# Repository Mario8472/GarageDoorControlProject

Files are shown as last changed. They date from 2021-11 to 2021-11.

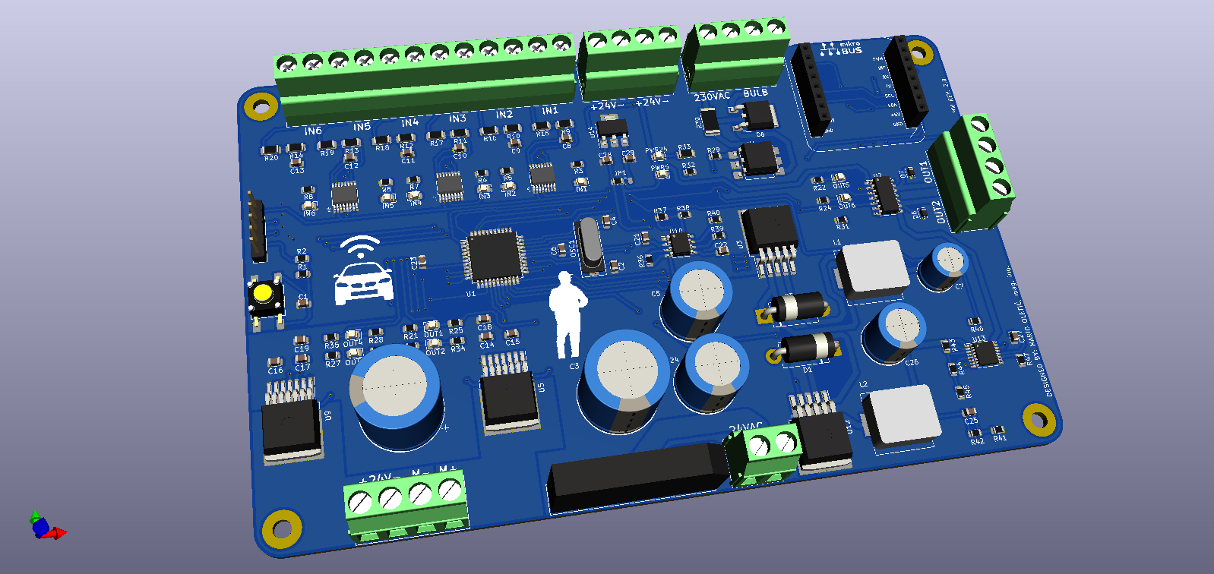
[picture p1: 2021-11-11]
KiCAD/Pictures/GarageDoorControl2.png

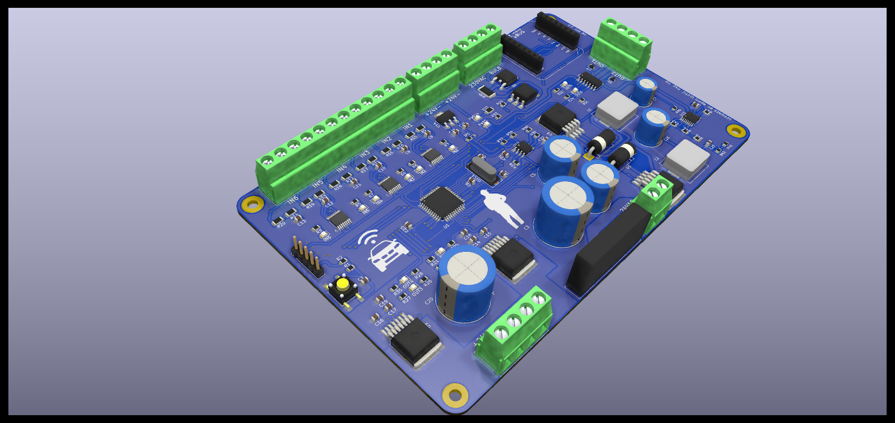
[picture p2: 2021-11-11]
KiCAD/Pictures/GarageDoorControl8.png

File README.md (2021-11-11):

# GarageDoorControlProject
Hardware and Software for Garage door control (retrofit) 

   Project:    Garage Door Control Unit
   MCU:        PIC18F45K22
   Hardware:   Garage Door Control PCB Card
   Software:   mikroC PRO for PIC18
   Author:     Mario Oletić
   
   Project description:
   -----------------------------------------------------------------------------
   This project is developed (both hardware and software) for replacing/retrofit
   the old garage door PCB. PCB has six input signals (24VDC level). Two of 
   them are used for starting the door movements (opening or closing). Doors can
   be started with radio switch (Input1) with 24VDC signal output or some other 
   common switch (Input2). Other four inputs are used for external capacitive or
   inductive sensors to determine door position - two for UP and DOWN positions 
   and two to determine a position of doors while approaching CLOSE or OPEN 
   positions. The last two positions are used for slowing the doors down. 
   Signals on INPUT1 and INPUT2 are switching between four working modes. MODE 0 
   and MODE2 are for stoping, MODE1 for opening and MODE3 for closing the doors.
   Outputs are used for controlling the 24V DC motor with PWM signals. Depending 
   on the door position, the motor can rotate with two different speeds (speed 
   depends on the PWM duty cycle) - one is for normal door speed and the other 
   (slower) is for approaching final positions. Also, when activating the door, 
   lights turn on. There are two outputs for 24V DC LED lights and one output 
   for 230V AC light bulb which is controlled via Triac. Triac is triggered with 
   OptoTriac IC with zero-cross detection circuit. Also, OptoTriac isolates 230V 
   AC system from the rest of the PCB low voltage systems. Lights will be turned 
   off after doors are stoped, no matter in what position, after a fixed period 
   of time passes. When doors are not moving, MCU goes into sleep mode with much 
   lower current consumption. When a new signal for activating the doors appears, 
   MCU wakes up.

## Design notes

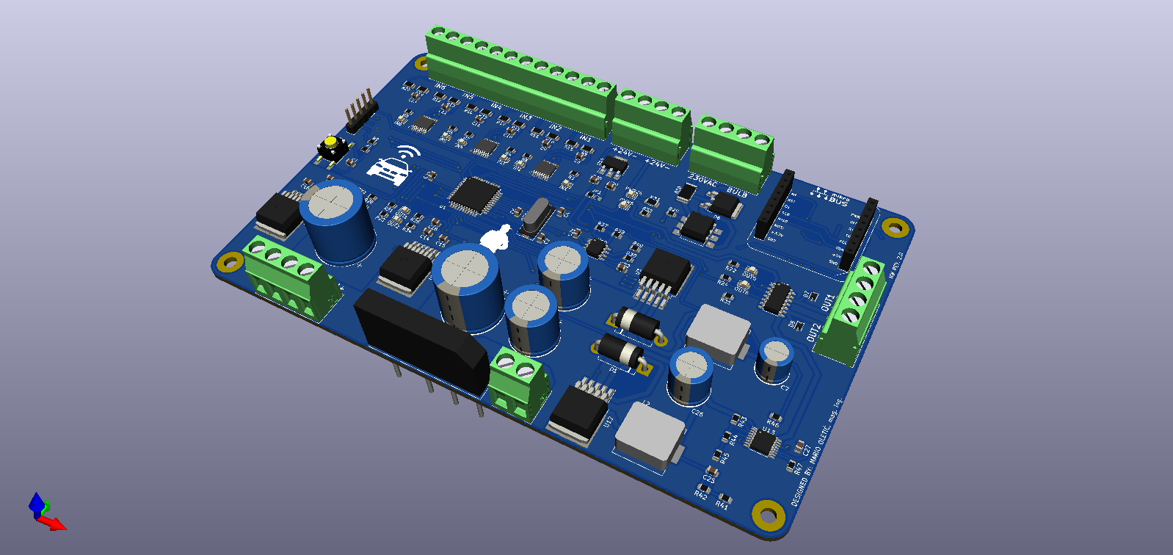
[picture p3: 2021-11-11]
KiCAD/Pictures/GarageDoorControl9.png

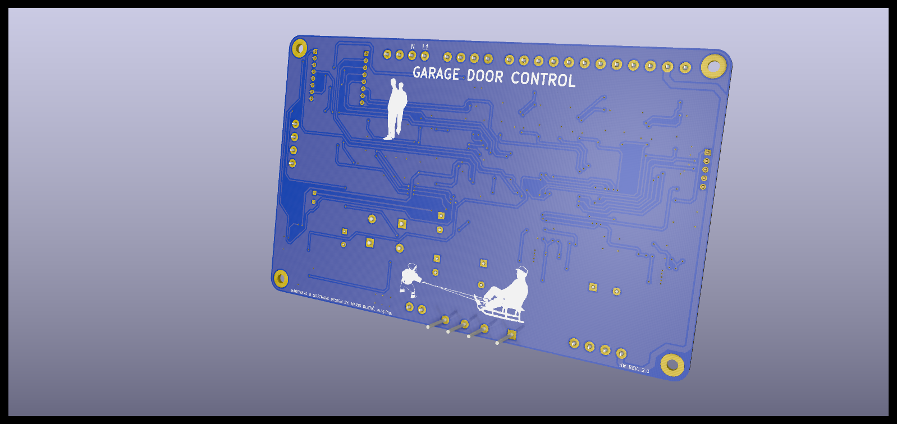
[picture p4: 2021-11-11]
KiCAD/Pictures/GarageDoorControl18.png

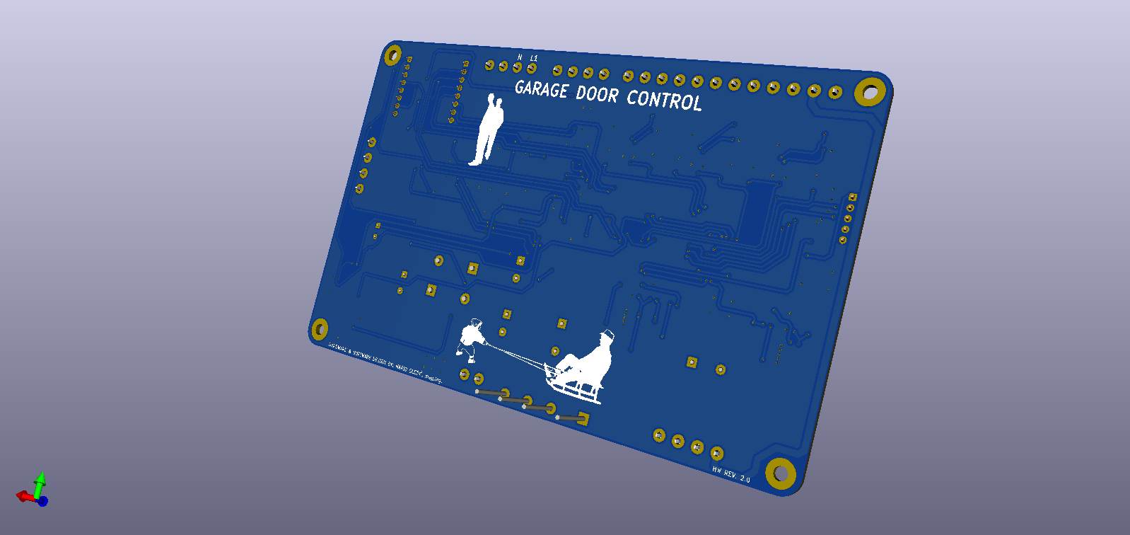
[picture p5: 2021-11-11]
KiCAD/Pictures/GarageDoorControl20.png

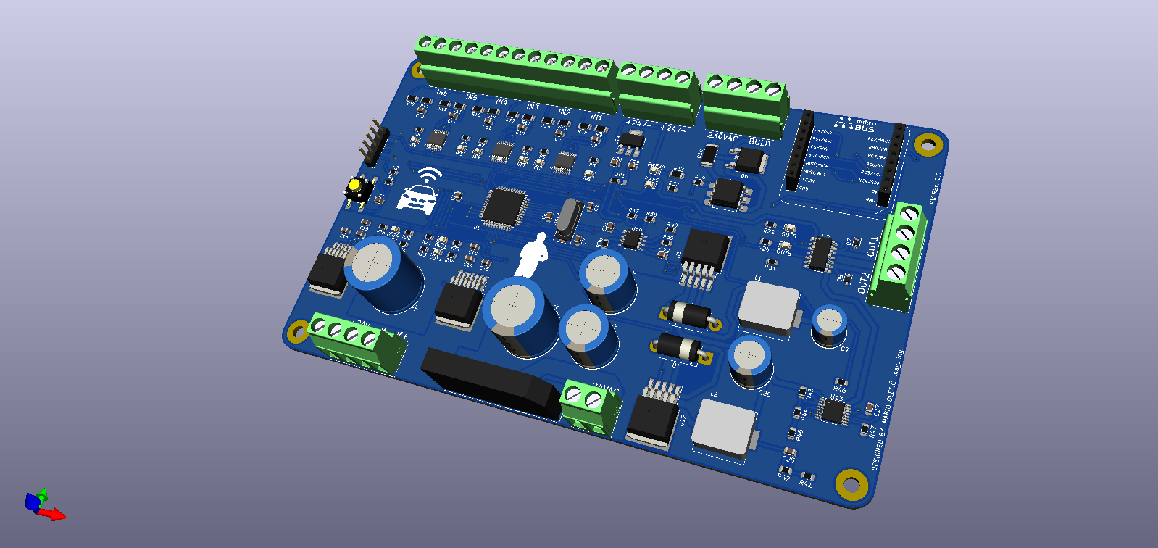
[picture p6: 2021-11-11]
KiCAD/Pictures/GarageDoorControl16.png

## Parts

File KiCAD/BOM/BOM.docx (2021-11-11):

BOM – Garage Door Control

Id | Designator | Package | Qt. | Designation
1 | G*** | dam5 | 1 | LOGO
2 | G*** | me_logo | 1 | LOGO
3 | G*** | m&d_logo | 1 | LOGO
4 | OSC1 | Crystal_SMD_HC49-SD | 1 | 8MHz
5 | U13 | HTSSOP-16-1EP_4.4x5mm_P0.65mm_EP3x3mm | 1 | TPS26600
6 | G*** | car_logo | 1 | LOGO
7 | C1,C6,C23 | C_0805_2012Metric | 3 | 100nF
8 | C2,C4 | C_0805_2012Metric | 2 | 22pF
9 | C3 | CP_Radial_D16.0mm_P7.50mm | 1 | 2200uF
10 | C7 | CP_Radial_D8.0mm_P3.50mm | 1 | 180uF
11 | C8,C9,C10,C11,C12,C13 | C_0805_2012Metric | 6 | 10nF
12 | CN1 | mikroBUS_socket | 1 | mikroBUS_socket
13 | D5,D1 | D_DO-201AD_P12.70mm_Horizontal | 2 | D_Schottky
14 | D6 | TO-252-2 | 1 | Q_TRIAC_A1A2G
15 | IN1,IN2,IN3,IN4,IN5,IN6, OUT1,OUT2,OUT3,OUT4, OUT5,OUT6,PWR5,PWR24 | LED_0805_2012Metric | 14 | LED
16 | J1 | PinHeader_1x05_P2.54mm_Vertical | 1 | Conn_01x05
17 | J2 | PCB_Screw_Terminal_5.08_12ways | 1 | Screw_Terminal_01x12
18 | L1 | HPI1206 | 1 | 68uH
19 | R1,R25,R27,R34,R35,R38, R39,R40,R46 | R_0805_2012Metric | 9 | 10k
20 | R2 | R_0805_2012Metric | 1 | 2k2
21 | R3,R4,R5,R6,R7,R8,R21,R22,R23,R24,R26,R28,R32 | R_0805_2012Metric | 13 | 4k7
22 | R9,R10,R11,R12,R13,R14, R15,R16,R17,R18,R19,R20 | R_1206_3216Metric | 12 | 330
23 | R29 | R_0805_2012Metric | 1 | 330
24 | R30 | R_2512_6332Metric | 1 | 200
25 | R31 | R_0805_2012Metric | 1 | 150
26 | R33 | R_1206_3216Metric | 1 | 10k
27 | RS1 | TACTSWITCH6x6 | 1 | SW_Push
28 | U2 | SOIC-14_3.9x8.7mm_P1.27mm | 1 | BTS5120G
29 | U3 | TO-263-5_TabPin3 | 1 | LM2596S-5
30 | U4 | SMDIP-6_W9.53mm | 1 | VO3062
31 | U6,U7,U8 | ISO1212 | 3 | ISO1212
32 | D7,D8 | D_SOD-323 | 2 | D
33 | C14,C15,C16,C17 | C_0805_2012Metric | 4 | 0.22uF
34 | C18,C19 | C_0805_2012Metric | 2 | 0.1uF
35 | C20 | CP_Radial_D16.0mm_P7.50mm | 1 | 1000uF
36 | U5,U9 | TO-263-7_TabPin4 | 2 | BTN8982TA
37 | C21 | C_0805_2012Metric | 1 | 0.1nF
38 | C22 | C_0805_2012Metric | 1 | 100uF
39 | R36 | R_0805_2012Metric | 1 | 100k
40 | R37 | R_0805_2012Metric | 1 | 47k
41 | U10 | SOIC-8_3.9x4.9mm_P1.27mm | 1 | TPS25921A
42 | H1,H2,H3,H4 | ScrewHoleM3 | 4 | ScrewHoleM3
43 | J4,J5,J6,J7 | PCB_Screw_Terminal_5.08_4ways | 4 | Screw_Terminal_01x04
44 | J3 | PCB_Screw_Terminal_5.08_2ways | 1 | Screw_Terminal_01x02
45 | U1 | TQFP-44_10x10mm_P0.8mm | 1 | PIC18F45K22
46 | U11 | DiodeBridge_GBI | 1 | GBI25B
47 | C5,C24 | CP_Radial_D12.5mm_P5.00mm | 2 | 680uF
48 | C25 | C_0805_2012Metric | 1 | 560pF
49 | C26 | CP_Radial_D10.0mm_P5.00mm | 1 | 150uF
50 | L2 | HPI1206 | 1 | 47uH
51 | R41 | R_0805_2012Metric | 1 | 1k
52 | R42 | R_0805_2012Metric | 1 | 18k5
53 | U12 | TO-263-5_TabPin3 | 1 | LM2596S-ADJ
54 | C27 | C_0805_2012Metric | 1 | 2.2uF
55 | R43 | R_0805_2012Metric | 1 | 715k
56 | R44 | R_0805_2012Metric | 1 | 20k
57 | R45 | R_0805_2012Metric | 1 | 30.1k
58 | R47 | R_0805_2012Metric | 1 | 5,36k
59 | C28 | C_0805_2012Metric | 1 | 0.47uF
60 | C29 | C_0805_2012Metric | 1 | 33uF
61 | JP1 | Jumper_0805 | 1 | SolderJumper_3_Open
62 | U14 | SOT-223 | 1 | LM3940

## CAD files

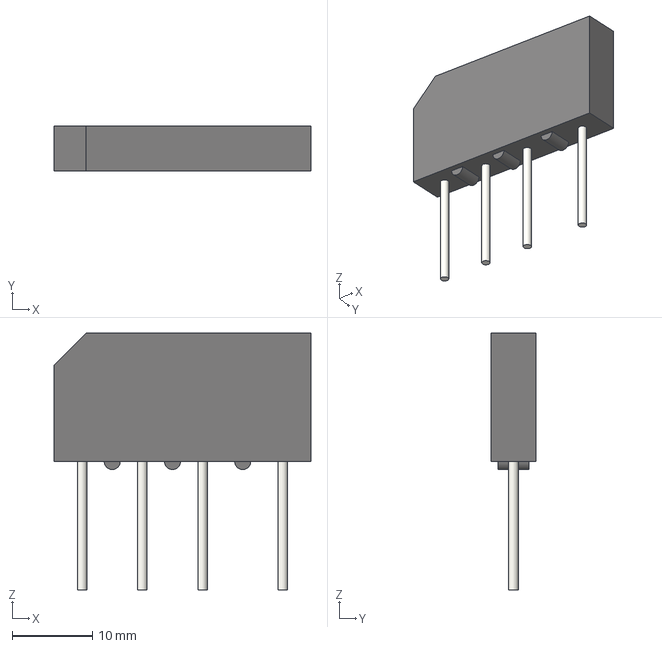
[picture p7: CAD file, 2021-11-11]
KiCAD/3D models/Diode_Bridge_32.0x5.6x17.0mm_P10.0mm_P7.5mm.step
32.0 x 5.60 x 32.0 mm

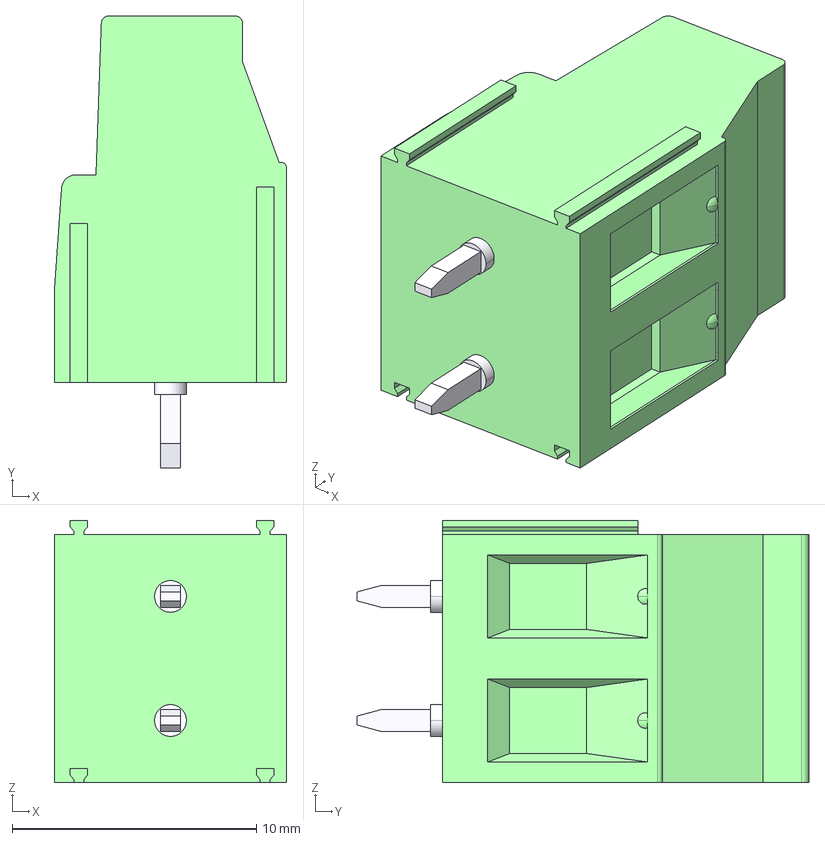
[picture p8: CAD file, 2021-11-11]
KiCAD/3D models/PCB Terminal 5.08 - 2way.stp
9.50 x 18.5 x 10.7 mm

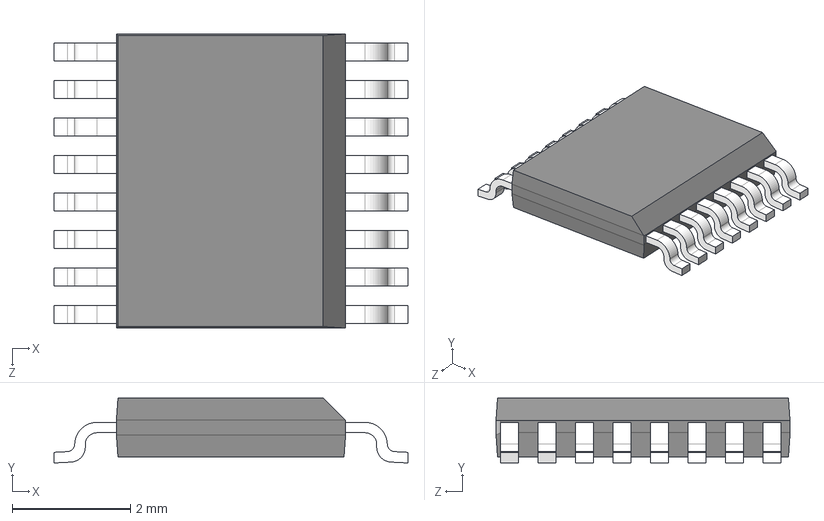
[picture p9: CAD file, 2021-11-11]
KiCAD/3D models/SSOP16.STEP
5.99 x 1.10 x 4.98 mm

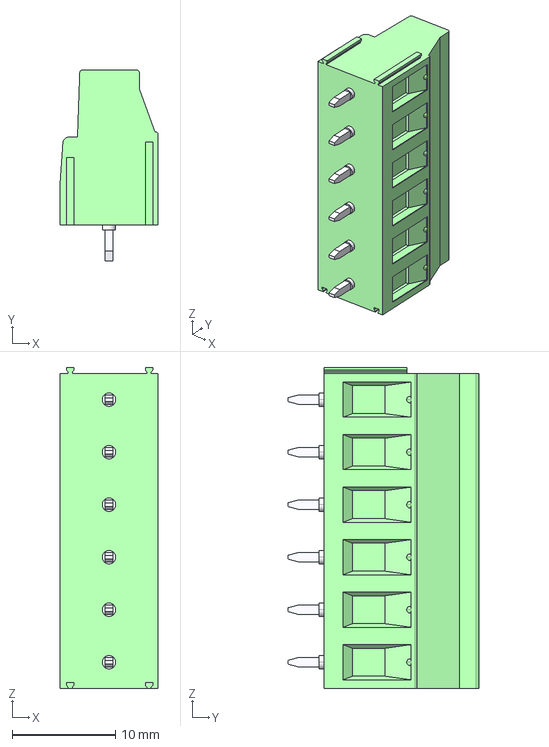
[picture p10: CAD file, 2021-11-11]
KiCAD/3D models/PCB Terminal 5.08 - 6way.stp
9.50 x 18.5 x 31.0 mm

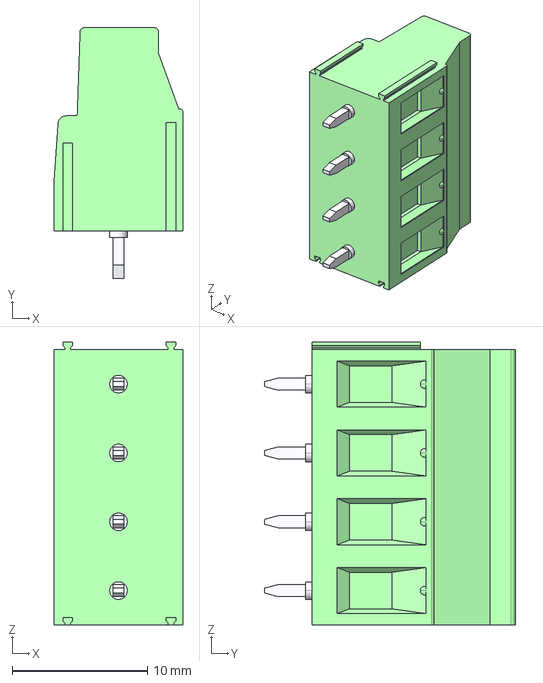
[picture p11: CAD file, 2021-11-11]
KiCAD/3D models/PCB Terminal 5.08 - 4way.stp
9.50 x 18.5 x 20.9 mm

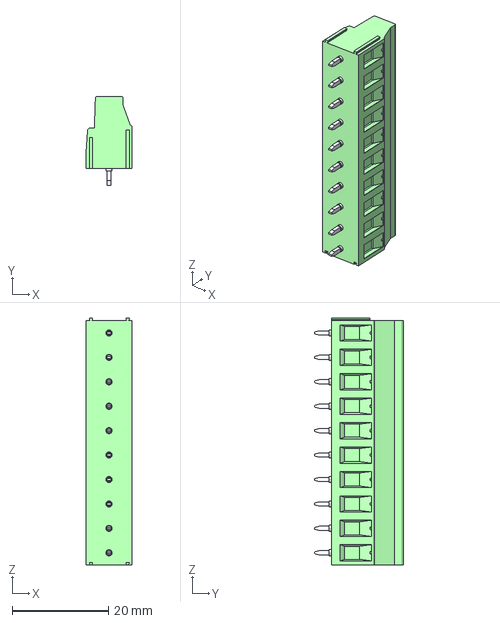
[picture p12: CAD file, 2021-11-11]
KiCAD/3D models/PCB Terminal 5.08 - 10way.stp
9.50 x 18.5 x 51.4 mm

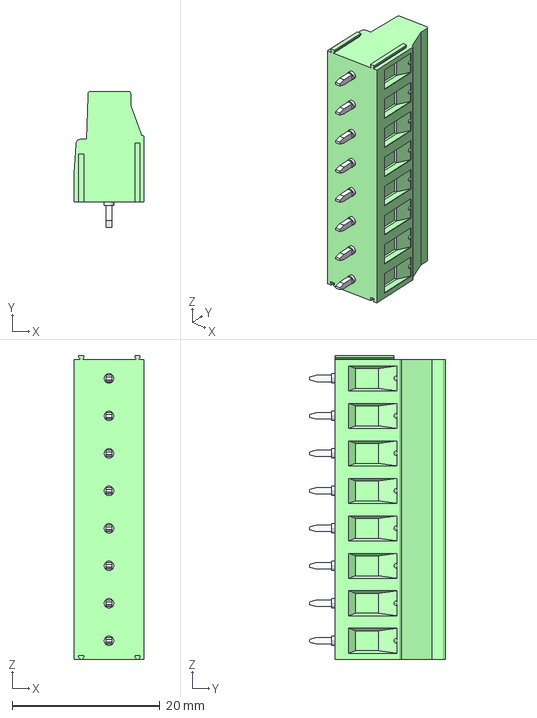
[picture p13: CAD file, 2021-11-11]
KiCAD/3D models/PCB Terminal 5.08 - 8way.stp
9.50 x 18.5 x 41.2 mm

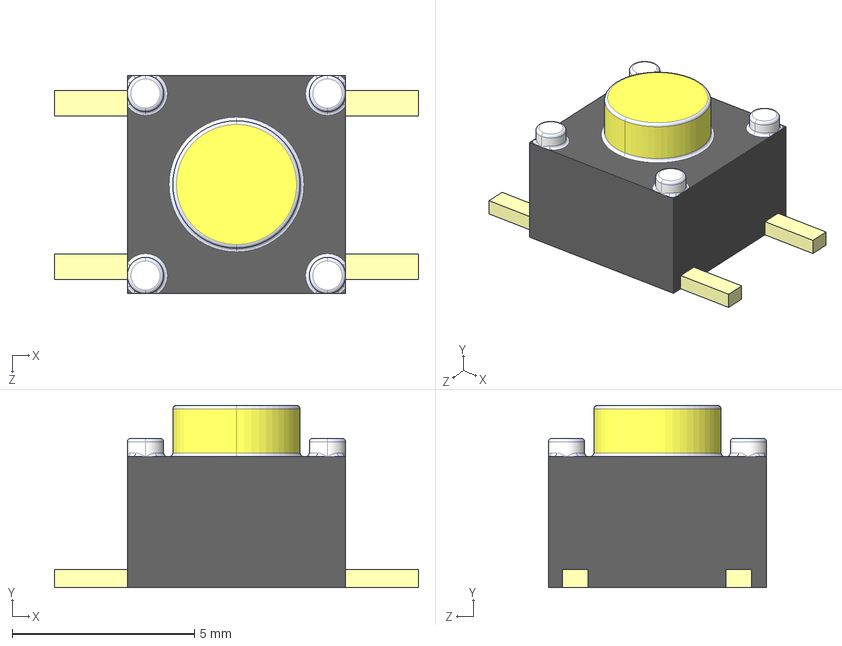
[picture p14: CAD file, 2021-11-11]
KiCAD/3D models/TACT SWITCH SMD 6X6.STEP
10.0 x 5.00 x 6.00 mm

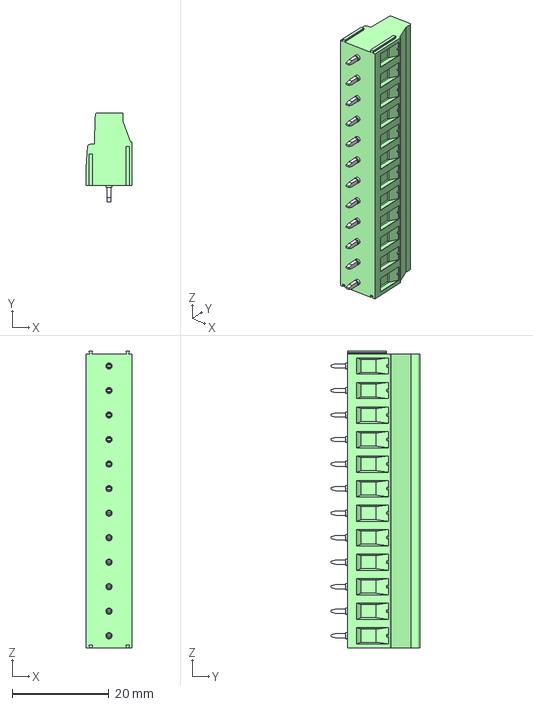
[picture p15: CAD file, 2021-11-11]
KiCAD/3D models/PCB Terminal 5.08 - 12way.stp
9.50 x 18.5 x 61.5 mm

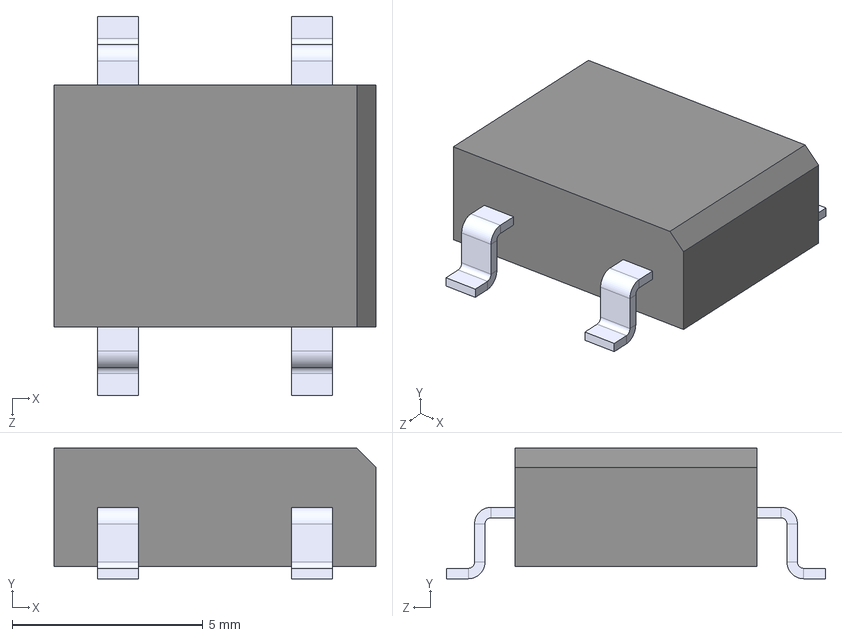
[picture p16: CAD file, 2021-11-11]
KiCAD/3D models/DB207S.SLDPRT.STEP
8.45 x 3.43 x 9.95 mm

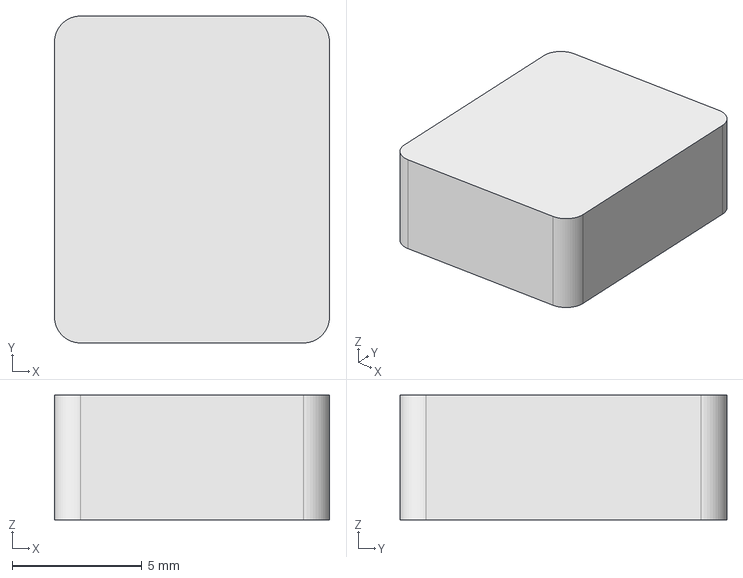
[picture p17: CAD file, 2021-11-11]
KiCAD/3D models/hpis.step
10.6 x 12.6 x 4.80 mm

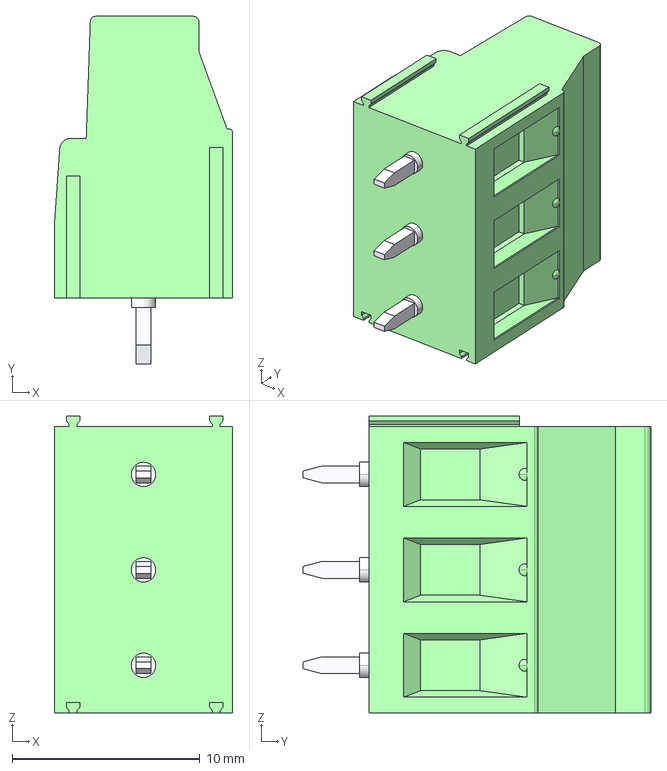
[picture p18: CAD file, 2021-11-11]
KiCAD/3D models/PCB Terminal 5.08 - 3way.stp
9.50 x 18.5 x 15.8 mm

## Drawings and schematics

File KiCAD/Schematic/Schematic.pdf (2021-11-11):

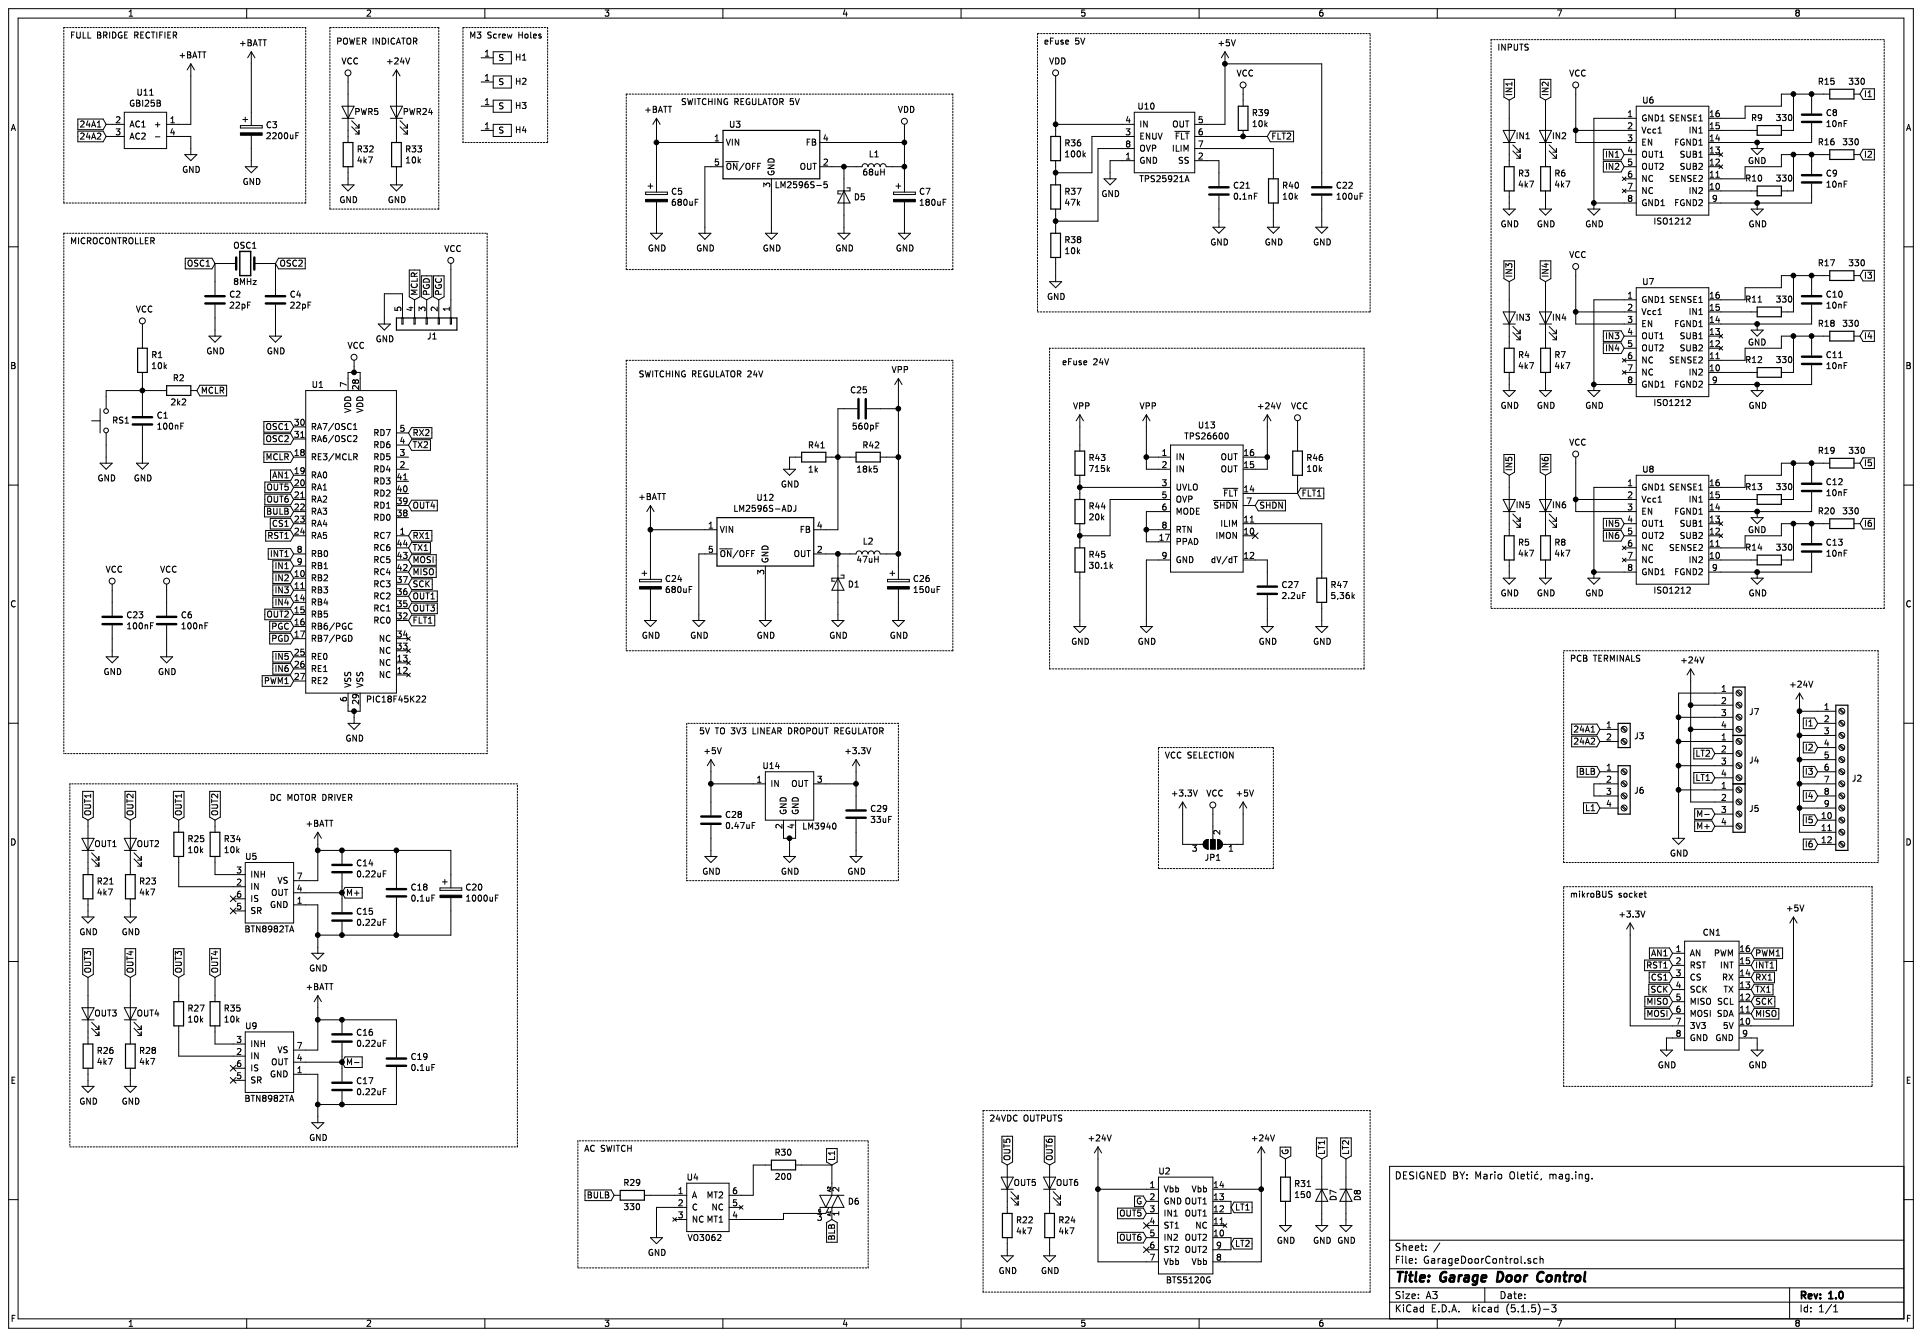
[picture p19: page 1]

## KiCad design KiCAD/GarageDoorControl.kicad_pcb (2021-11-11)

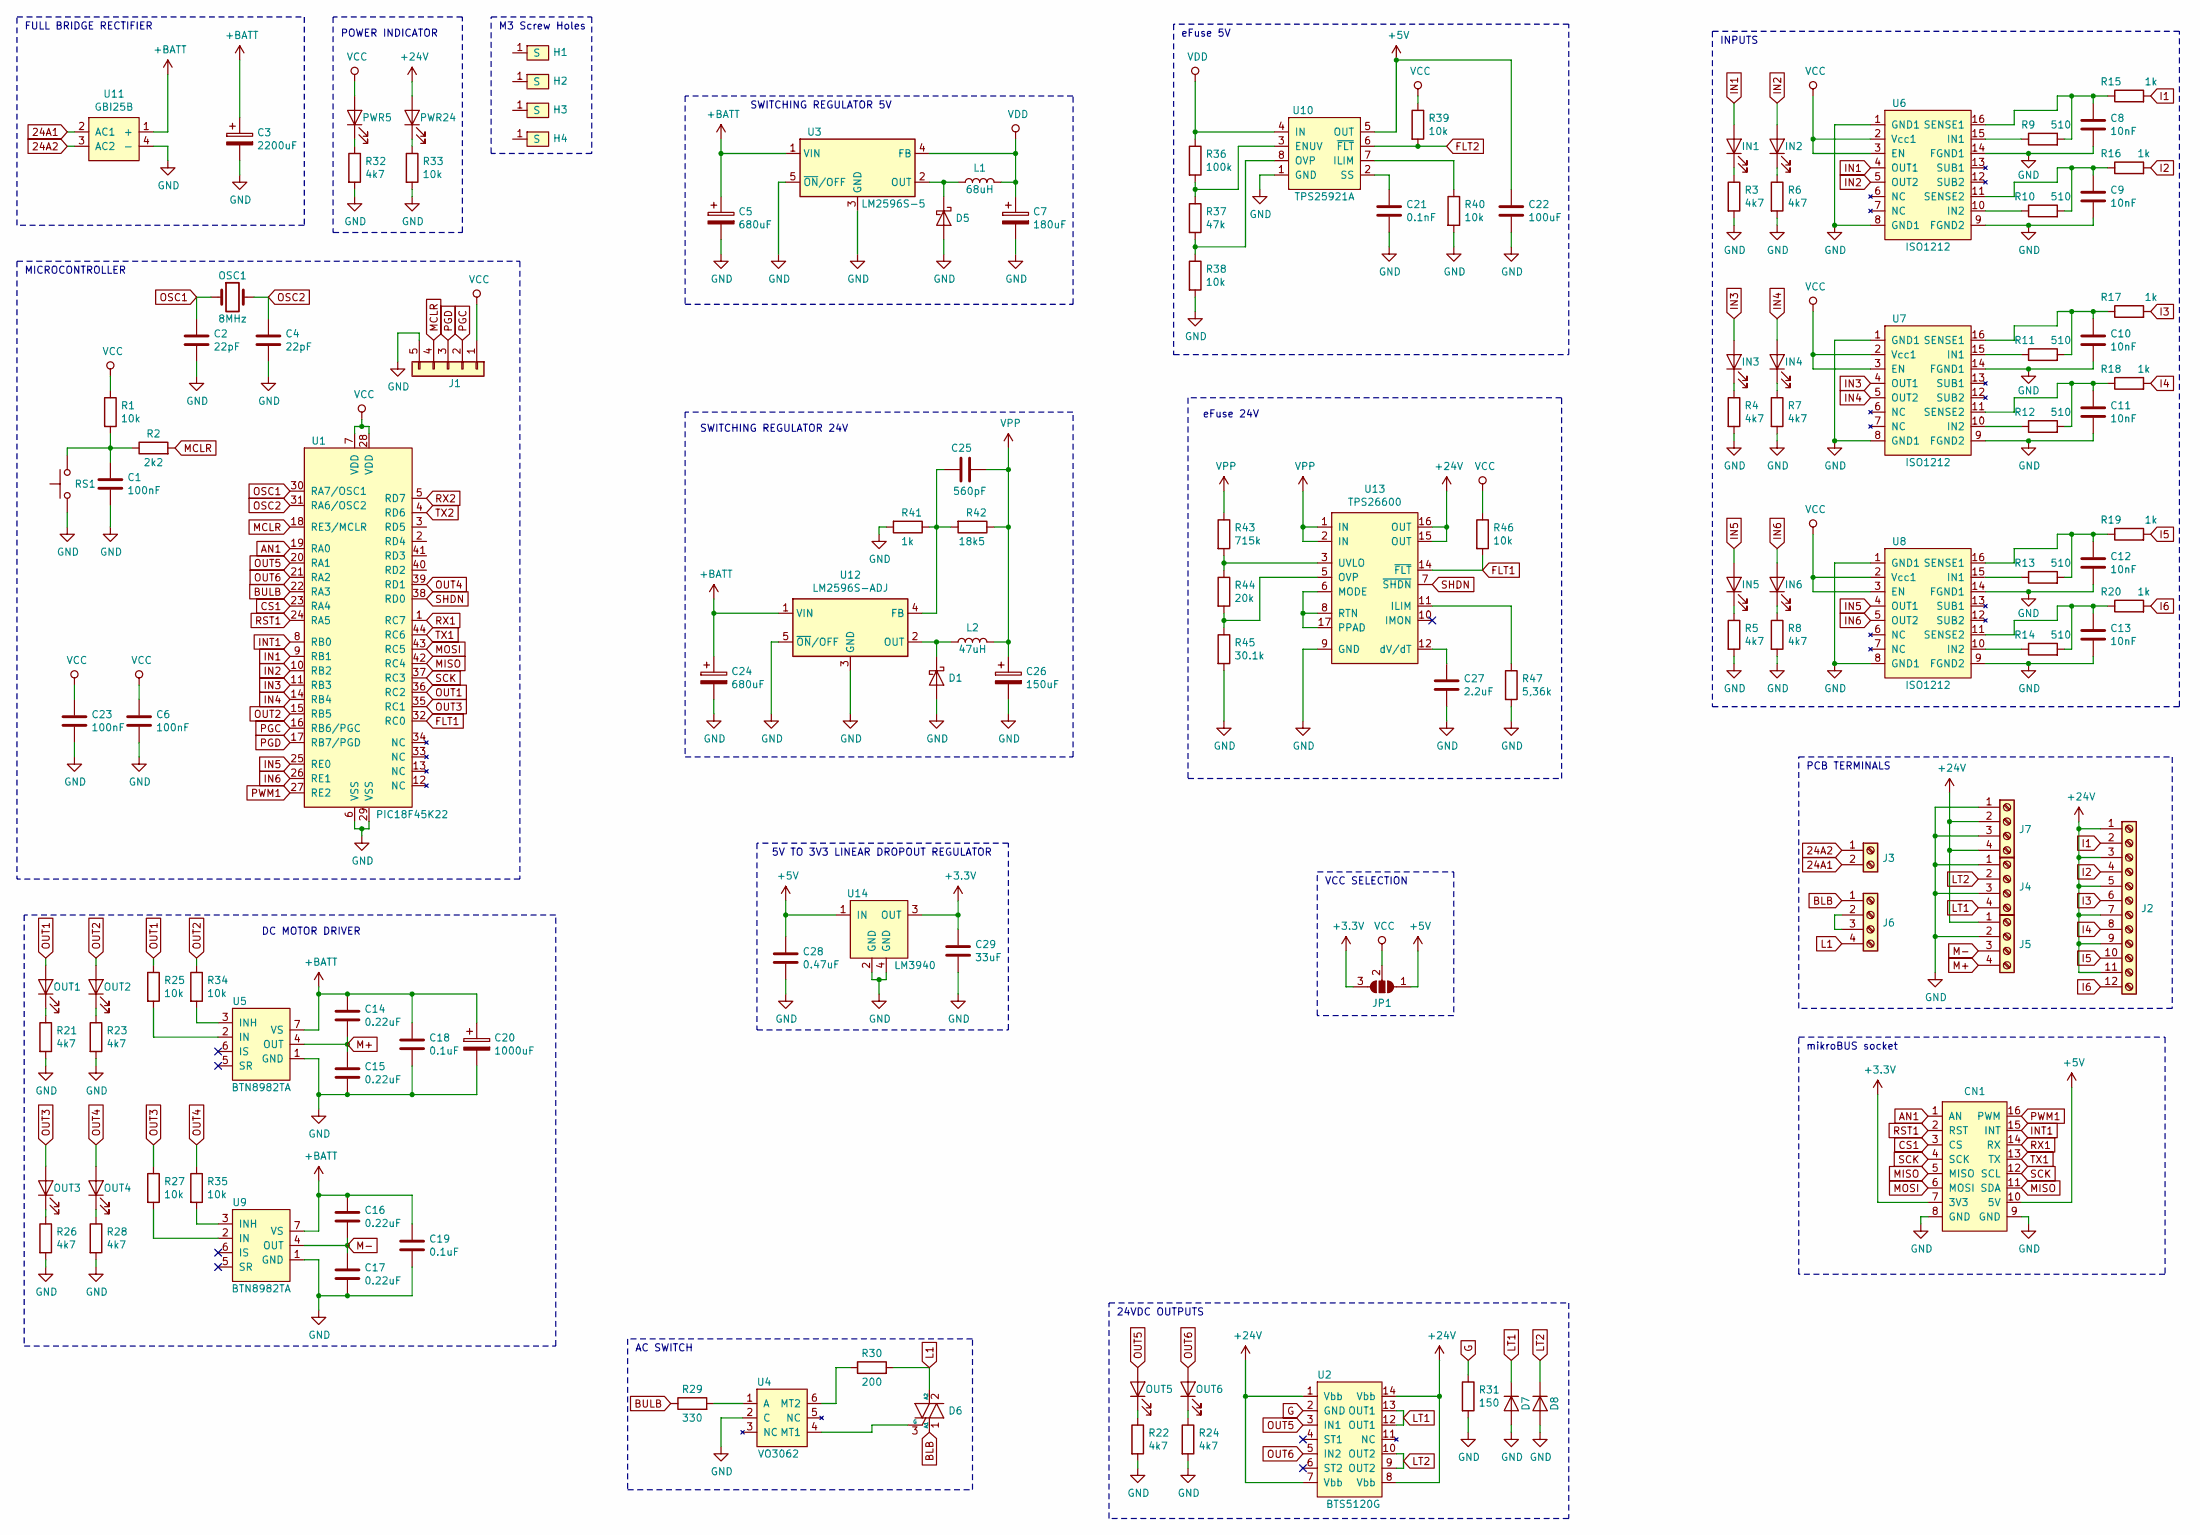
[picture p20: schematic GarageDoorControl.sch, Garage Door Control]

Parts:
C1, C6, C23: 100nF; C_0805_2012Metric
C2, C4: 22pF; C_0805_2012Metric
C3: 2200uF; CP_Radial_D16.0mm_P7.50mm
C5, C24: 680uF; CP_Radial_D12.5mm_P5.00mm
C7: 180uF; CP_Radial_D8.0mm_P3.50mm
C8, C9, C10, C11, C12, C13: 10nF; C_0805_2012Metric
C14, C15, C16, C17: 0.22uF; C_0805_2012Metric
C18, C19: 0.1uF; C_0805_2012Metric
C20: 1000uF; CP_Radial_D16.0mm_P7.50mm
C21: 0.1nF; C_0805_2012Metric
C22: 100uF; C_0805_2012Metric
C25: 560pF; C_0805_2012Metric
C26: 150uF; CP_Radial_D10.0mm_P5.00mm
C27: 2.2uF; C_0805_2012Metric
C28: 0.47uF; C_0805_2012Metric
C29: 33uF; C_0805_2012Metric
CN1: mikroBUS_socket
D1, D5: D_Schottky; D_DO-201AD_P12.70mm_Horizontal
D6: Q_TRIAC_A1A2G; TO-252-2
D7, D8: D; D_SOD-323
H1, H2, H3, H4: ScrewHoleM3
IN1, IN2, IN3, IN4, IN5, IN6: LED; LED_0805_2012Metric
J1: Conn_01x05; PinHeader_1x05_P2.54mm_Vertical
J2: Screw_Terminal_01x12; PCB_Screw_Terminal_5.08_12ways
J3: Screw_Terminal_01x02; PCB_Screw_Terminal_5.08_2ways
J4, J5, J6, J7: Screw_Terminal_01x04; PCB_Screw_Terminal_5.08_4ways
JP1: SolderJumper_3_Open; Jumper_0805
L1: 68uH; HPI1206
L2: 47uH; HPI1206
OSC1: 8MHz; Crystal_SMD_HC49-SD
OUT1, OUT2, OUT3, OUT4, OUT5, OUT6: LED; LED_0805_2012Metric
PWR5, PWR24: LED; LED_0805_2012Metric
R1, R25, R27, R34, R35, R38, R39, R40, R46: 10k; R_0805_2012Metric
R2: 2k2; R_0805_2012Metric
R3, R4, R5, R6, R7, R8, R21, R22, R23, R24, R26, R28, R32: 4k7; R_0805_2012Metric
R9, R10, R11, R12, R13, R14: 510; R_1206_3216Metric
R15, R16, R17, R18, R19, R20: 1k; R_1206_3216Metric
R29: 330; R_0805_2012Metric
R30: 200; R_2512_6332Metric
R31: 150; R_0805_2012Metric
R33: 10k; R_1206_3216Metric
R36: 100k; R_0805_2012Metric
R37: 47k; R_0805_2012Metric
R41: 1k; R_0805_2012Metric
R42: 18k5; R_0805_2012Metric
R43: 715k; R_0805_2012Metric
R44: 20k; R_0805_2012Metric
R45: 30.1k; R_0805_2012Metric
R47: 5,36k; R_0805_2012Metric
RS1: SW_Push; TACTSWITCH6x6
U1: PIC18F45K22; TQFP-44_10x10mm_P0.8mm
U2: BTS5120G; SOIC-14_3.9x8.7mm_P1.27mm
U3: LM2596S-5; TO-263-5_TabPin3
U4: VO3062; SMDIP-6_W9.53mm
U5, U9: BTN8982TA; TO-263-7_TabPin4
U6, U7, U8: ISO1212
U10: TPS25921A; SOIC-8_3.9x4.9mm_P1.27mm
U11: GBI25B; DiodeBridge_GBI
U12: LM2596S-ADJ; TO-263-5_TabPin3
U13: TPS26600; HTSSOP-16-1EP_4.4x5mm_P0.65mm_EP3x3mm
U14: LM3940; SOT-223

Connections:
24A1: J3.2, U11.2 (AC1)
24A2: J3.1, U11.3 (AC2)
+3V3: C29.1, CN1.7 (3V3), JP1.3 (B), U14.3 (OUT)
+5V: C22.1, C28.1, CN1.10 (5V), JP1.1 (A), U10.5 (OUT), U14.1 (IN)
+24V: J2.1, J2.3, J2.5, J2.7, J2.9, J2.11, J5.1, J7.2, J7.4, PWR24.2 (A), U2.1 (Vbb), U2.7 (Vbb), U2.8 (Vbb), U2.14 (Vbb), U13.15 (OUT), U13.16 (OUT)
+BATT: C3.1, C5.1, C14.1, C16.1, C18.1, C19.1, C20.1, C24.1, U3.1 (VIN), U5.7 (VS), U9.7 (VS), U11.1 (+), U12.1 (VIN)
AN1: CN1.1 (AN), U1.19 (RA0)
BLB: D6.1 (A1), J6.1
BULB: R29.1, U1.22 (RA3)
CS1: CN1.3 (CS), U1.23 (RA4)
FLT1: R46.2, U1.32 (RC0), U13.14 (~FLT)
FLT2: R39.2, U10.6 (~FLT)
G: R31.1, U2.2 (GND)
GND: C1.2, C2.2, C3.2, C4.2, C5.2, C6.2, C7.2, C8.2, C9.2, C10.2, C11.2, C12.2, C13.2, C15.2, C17.2, C18.2, C19.2, C20.2, C21.2, C22.2, C23.2, C24.2, C26.2, C27.2, C28.2, C29.2, CN1.8 (GND), CN1.9 (GND), D1.2 (A), D5.2 (A), D7.2 (A), D8.2 (A), J1.5, J4.1, J4.3, J5.2, J7.1, J7.3, R3.2, R4.2, R5.2, R6.2, R7.2, R8.2, R21.2, R22.2, R23.2, R24.2, R26.2, R28.2, R31.2, R32.2, R33.2, R38.2, R40.2, R41.2, R45.2, R47.2, RS1.1, U1.6 (VSS), U1.29 (VSS), U3.3 (GND), U3.5 (~ON~/OFF), U4.2 (C), U5.1 (GND), U6.1 (GND1), U6.8 (GND1), U6.9 (FGND2), U6.14 (FGND1), U7.1 (GND1), U7.8 (GND1), U7.9 (FGND2), U7.14 (FGND1), U8.1 (GND1), U8.8 (GND1), U8.9 (FGND2), U8.14 (FGND1), U9.1 (GND), U10.1 (GND), U11.4 (-), U12.3 (GND), U12.5 (~ON~/OFF), U13.9 (GND), U14.2 (GND), U14.4 (GND)
I1: J2.2, R15.2
I2: J2.4, R16.2
I3: J2.6, R17.2
I4: J2.8, R18.2
I5: J2.10, R19.2
I6: J2.12, R20.2
IN1: IN1.2 (A), U1.9 (RB1), U6.4 (OUT1)
IN2: IN2.2 (A), U1.10 (RB2), U6.5 (OUT2)
IN3: IN3.2 (A), U1.11 (RB3), U7.4 (OUT1)
IN4: IN4.2 (A), U1.14 (RB4), U7.5 (OUT2)
IN5: IN5.2 (A), U1.25 (RE0), U8.4 (OUT1)
IN6: IN6.2 (A), U1.26 (RE1), U8.5 (OUT2)
INT1: CN1.15 (INT), U1.8 (RB0)
L1: D6.2 (A2), J6.4, R30.2
LT1: D7.1 (K), J4.4, U2.12 (OUT1), U2.13 (OUT1)
LT2: D8.1 (K), J4.2, U2.9 (OUT2), U2.10 (OUT2)
M+: C14.2, C15.1, J5.4, U5.4 (OUT)
M-: C16.2, C17.1, J5.3, U9.4 (OUT)
MCLR: J1.4, R2.2, U1.18 (RE3/MCLR)
MISO: CN1.5 (MISO), CN1.11 (SDA), U1.42 (RC4)
MOSI: CN1.6 (MOSI), U1.43 (RC5)
unnamed: C1.1, R1.2, R2.1, RS1.2
unnamed: C8.1, R9.2, R15.1, U6.16 (SENSE1)
unnamed: C9.1, R10.2, R16.1, U6.11 (SENSE2)
unnamed: C10.1, R11.2, R17.1, U7.16 (SENSE1)
unnamed: C11.1, R12.2, R18.1, U7.11 (SENSE2)
unnamed: C12.1, R13.2, R19.1, U8.16 (SENSE1)
unnamed: C13.1, R14.2, R20.1, U8.11 (SENSE2)
unnamed: C21.1, U10.2 (SS)
unnamed: C25.1, R41.1, R42.2, U12.4 (FB)
unnamed: C27.1, U13.12 (dV/dT)
unnamed: D1.1 (K), L2.1, U12.2 (OUT)
unnamed: D5.1 (K), L1.1, U3.2 (OUT)
unnamed: D6.3 (G), U4.4 (MT1)
unnamed: IN1.1 (K), R3.1
unnamed: IN2.1 (K), R6.1
unnamed: IN3.1 (K), R4.1
unnamed: IN4.1 (K), R7.1
unnamed: IN5.1 (K), R5.1
unnamed: IN6.1 (K), R8.1
unnamed: J6.2, J6.3
unnamed: OUT1.1 (K), R21.1
unnamed: OUT2.1 (K), R23.1
unnamed: OUT3.1 (K), R26.1
unnamed: OUT4.1 (K), R28.1
unnamed: OUT5.1 (K), R22.1
unnamed: OUT6.1 (K), R24.1
unnamed: PWR5.1 (K), R32.1
unnamed: PWR24.1 (K), R33.1
unnamed: R9.1, U6.15 (IN1)
unnamed: R10.1, U6.10 (IN2)
unnamed: R11.1, U7.15 (IN1)
unnamed: R12.1, U7.10 (IN2)
unnamed: R13.1, U8.15 (IN1)
unnamed: R14.1, U8.10 (IN2)
unnamed: R25.2, U5.2 (IN)
unnamed: R27.2, U9.2 (IN)
unnamed: R29.2, U4.1 (A)
unnamed: R30.1, U4.6 (MT2)
unnamed: R34.2, U5.3 (INH)
unnamed: R35.2, U9.3 (INH)
unnamed: R36.2, R37.1, U10.3 (ENUV)
unnamed: R37.2, R38.1, U10.8 (OVP)
unnamed: R40.1, U10.7 (ILIM)
unnamed: R43.2, R44.1, U13.3 (UVLO)
unnamed: R44.2, R45.1, U13.5 (OVP)
unnamed: R47.1, U13.11 (ILIM)
unnamed: U13.6 (MODE), U13.8 (RTN), U13.17 (PPAD)
OSC1: C2.1, OSC1.1, U1.30 (RA7/OSC1)
OSC2: C4.1, OSC1.2, U1.31 (RA6/OSC2)
OUT1: OUT1.2 (A), R25.1, U1.36 (RC2)
OUT2: OUT2.2 (A), R34.1, U1.15 (RB5)
OUT3: OUT3.2 (A), R27.1, U1.35 (RC1)
OUT4: OUT4.2 (A), R35.1, U1.39 (RD1)
OUT5: OUT5.2 (A), U1.20 (RA1), U2.3 (IN1)
OUT6: OUT6.2 (A), U1.21 (RA2), U2.5 (IN2)
PGC: J1.2, U1.16 (RB6/PGC)
PGD: J1.3, U1.17 (RB7/PGD)
PWM1: CN1.16 (PWM), U1.27 (RE2)
RST1: CN1.2 (RST), U1.24 (RA5)
RX1: CN1.14 (RX), U1.1 (RC7)
RX2: U1.5 (RD7)
SCK: CN1.4 (SCK), CN1.12 (SCL), U1.37 (RC3)
SHDN: U1.38 (RD0), U13.7 (~SHDN)
TX1: CN1.13 (TX), U1.44 (RC6)
TX2: U1.4 (RD6)
VCC: C6.1, C23.1, J1.1, JP1.2 (C), PWR5.2 (A), R1.1, R39.1, R46.1, U1.7 (VDD), U1.28 (VDD), U6.2 (Vcc1), U6.3 (EN), U7.2 (Vcc1), U7.3 (EN), U8.2 (Vcc1), U8.3 (EN)
VDD: C7.1, L1.2, R36.1, U3.4 (FB), U10.4 (IN)
VPP: C25.2, C26.1, L2.2, R42.1, R43.1, U13.1 (IN), U13.2 (IN)

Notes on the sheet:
FULL BRIDGE RECTIFIER
SWITCHING REGULATOR 5V
MICROCONTROLLER
INPUTS
DC MOTOR DRIVER
24VDC OUTPUTS
AC SWITCH
PCB TERMINALS
mikroBUS socket
POWER INDICATOR
eFuse 5V
M3 Screw Holes
SWITCHING REGULATOR 24V
eFuse 24V
5V TO 3V3 LINEAR DROPOUT REGULATOR
VCC SELECTION

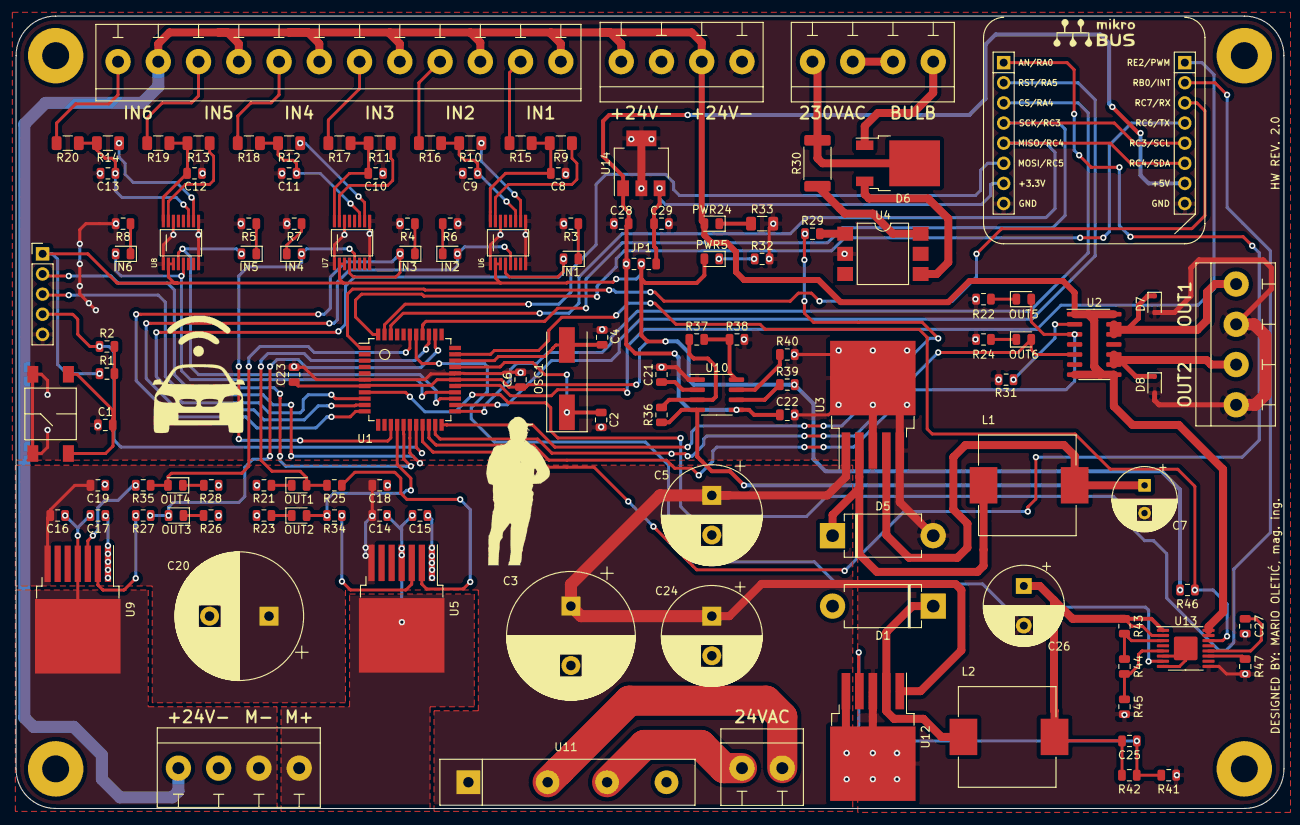
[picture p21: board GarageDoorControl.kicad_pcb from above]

Board: 2 copper layers, 160.0 x 100.0 mm, 126 parts (0 on the bottom side), 101 nets.

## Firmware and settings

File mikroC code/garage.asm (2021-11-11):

_Sleep_Start:

;garage.c,50 :: 		void Sleep_Start()
;garage.c,52 :: 		OSCCON.IDLEN = 0;
	BCF         OSCCON+0, 7 
;garage.c,53 :: 		asm sleep;
	SLEEP
;garage.c,54 :: 		}
L_end_Sleep_Start:
	RETURN      0
; end of _Sleep_Start

_interrupt:

;garage.c,57 :: 		void interrupt()
;garage.c,60 :: 		if(INTCON.TMR0IF)
	BTFSS       INTCON+0, 2 
	GOTO        L_interrupt0
;garage.c,62 :: 		cnt++;
	INCF        _cnt+0, 1 
;garage.c,64 :: 		TMR0L = 0x00;
	CLRF        TMR0L+0 
;garage.c,65 :: 		TMR0H = 0x00;
	CLRF        TMR0H+0 
;garage.c,67 :: 		if(cnt >= 1)
	MOVLW       1
	SUBWF       _cnt+0, 0 
	BTFSS       STATUS+0, 0 
	GOTO        L_interrupt1
;garage.c,70 :: 		T0CON.TMR0ON = 0;
	BCF         T0CON+0, 7 
;garage.c,73 :: 		BULB = 0;
	BCF         LATA+0, 3 
;garage.c,74 :: 		LED_LIGHT1 = 0;
	BCF         LATA+0, 1 
;garage.c,75 :: 		LED_LIGHT2 = 0;
	BCF         LATA+0, 2 
;garage.c,77 :: 		Sleep_Start();
	CALL        _Sleep_Start+0, 0
;garage.c,79 :: 		cnt = 0;
	CLRF        _cnt+0 
;garage.c,80 :: 		}
L_interrupt1:
;garage.c,81 :: 		INTCON.TMR0IF = 0;
	BCF         INTCON+0, 2 
;garage.c,82 :: 		}
L_interrupt0:
;garage.c,85 :: 		if(INTCON3.INT1IF)
	BTFSS       INTCON3+0, 0 
	GOTO        L_interrupt2
;garage.c,87 :: 		INTCON3.INT1IF = 0;
	BCF         INTCON3+0, 0 
;garage.c,88 :: 		}
L_interrupt2:
;garage.c,91 :: 		if(INTCON3.INT2IF)
	BTFSS       INTCON3+0, 1 
	GOTO        L_interrupt3
;garage.c,93 :: 		INTCON3.INT2IF = 0;
	BCF         INTCON3+0, 1 
;garage.c,94 :: 		}
L_interrupt3:
;garage.c,95 :: 		}
L_end_interrupt:
L__interrupt79:
	RETFIE      1
; end of _interrupt

_MCU_Init:

;garage.c,98 :: 		void MCU_Init()
;garage.c,100 :: 		ANSELA=0x00;
	CLRF        ANSELA+0 
;garage.c,101 :: 		ANSELB=0x00;
	CLRF        ANSELB+0 
;garage.c,102 :: 		ANSELC=0x00;
	CLRF        ANSELC+0 
;garage.c,103 :: 		ANSELD=0x00;
	CLRF        ANSELD+0 
;garage.c,104 :: 		ANSELE=0x00;
	CLRF        ANSELE+0 
;garage.c,105 :: 		TRISA=0x00;
	CLRF        TRISA+0 
;garage.c,106 :: 		TRISB=0b00011111;
	MOVLW       31
	MOVWF       TRISB+0 
;garage.c,107 :: 		TRISC=0x00;
	CLRF        TRISC+0 
;garage.c,108 :: 		TRISD=0x00;
	CLRF        TRISD+0 
;garage.c,109 :: 		TRISE=0b00000011;
	MOVLW       3
	MOVWF       TRISE+0 
;garage.c,110 :: 		LATA=0x00;
	CLRF        LATA+0 
;garage.c,111 :: 		LATB=0x00;
	CLRF        LATB+0 
;garage.c,112 :: 		LATC=0x00;
	CLRF        LATC+0 
;garage.c,113 :: 		LATD=0x00;
	CLRF        LATD+0 
;garage.c,114 :: 		LATE=0x00;
	CLRF        LATE+0 
;garage.c,116 :: 		PWM1_Init(5000);
	BSF         T2CON+0, 0, 0
	BCF         T2CON+0, 1, 0
	MOVLW       99
	MOVWF       PR2+0, 0
	CALL        _PWM1_Init+0, 0
;garage.c,117 :: 		PWM2_Init(5000);
	BSF         T2CON+0, 0, 0
	BCF         T2CON+0, 1, 0
	MOVLW       99
	MOVWF       PR2+0, 0
	CALL        _PWM2_Init+0, 0
;garage.c,119 :: 		Delay_ms(150);
	MOVLW       2
	MOVWF       R11, 0
	MOVLW       134
	MOVWF       R12, 0
	MOVLW       153
	MOVWF       R13, 0
L_MCU_Init4:
	DECFSZ      R13, 1, 1
	BRA         L_MCU_Init4
	DECFSZ      R12, 1, 1
	BRA         L_MCU_Init4
	DECFSZ      R11, 1, 1
	BRA         L_MCU_Init4
;garage.c,120 :: 		}
L_end_MCU_Init:
	RETURN      0
; end of _MCU_Init

_Flags_Init:

;garage.c,123 :: 		void Flags_Init()
;garage.c,125 :: 		start_state = 0;
	BCF         _start_state+0, BitPos(_start_state+0) 
;garage.c,126 :: 		start_state2 = 0;
	BCF         _start_state2+0, BitPos(_start_state2+0) 
;garage.c,127 :: 		mode = 0;
	CLRF        _mode+0 
;garage.c,128 :: 		door_down = 0;
	BCF         _door_down+0, BitPos(_door_down+0) 
;garage.c,129 :: 		door_up = 0;
	BCF         _door_up+0, BitPos(_door_up+0) 
;garage.c,130 :: 		slow_opening = 0;
	BCF         _slow_opening+0, BitPos(_slow_opening+0) 
;garage.c,131 :: 		slow_closing = 0;
	BCF         _slow_closing+0, BitPos(_slow_closing+0) 
;garage.c,132 :: 		zoneA = 1;
	BSF         _zoneA+0, BitPos(_zoneA+0) 
;garage.c,133 :: 		zoneB = 0;
	BCF         _zoneB+0, BitPos(_zoneB+0) 
;garage.c,134 :: 		zoneC = 0;
	BCF         _zoneC+0, BitPos(_zoneC+0) 
;garage.c,135 :: 		}
L_end_Flags_Init:
	RETURN      0
; end of _Flags_Init

_Door_Stop:

;garage.c,138 :: 		void Door_Stop()
;garage.c,140 :: 		PWM1_Stop();
	CALL        _PWM1_Stop+0, 0
;garage.c,141 :: 		PWM2_Stop();
	CALL        _PWM2_Stop+0, 0
;garage.c,143 :: 		BRIDGE1_ENABLE = 0;
	BCF         LATB+0, 5 
;garage.c,144 :: 		BRIDGE2_ENABLE = 0;
	BCF         LATD+0, 1 
;garage.c,145 :: 		DIRECTION1 = 0;
	BCF         LATC+0, 2 
;garage.c,146 :: 		DIRECTION2 = 0;
	BCF         LATC+0, 1 
;garage.c,147 :: 		}
L_end_Door_Stop:
	RETURN      0
; end of _Door_Stop

_Door_Open:

;garage.c,150 :: 		void Door_Open()
;garage.c,152 :: 		BRIDGE1_ENABLE = 1;
	BSF         LATB+0, 5 
;garage.c,153 :: 		BRIDGE2_ENABLE = 1;
	BSF         LATD+0, 1 
;garage.c,155 :: 		PWM1_Set_Duty(90);
	MOVLW       90
	MOVWF       FARG_PWM1_Set_Duty_new_duty+0 
	CALL        _PWM1_Set_Duty+0, 0
;garage.c,156 :: 		PWM1_Start();
	CALL        _PWM1_Start+0, 0
;garage.c,157 :: 		}
L_end_Door_Open:
	RETURN      0
; end of _Door_Open

_Door_Open_Slow:

;garage.c,160 :: 		void Door_Open_Slow()
;garage.c,162 :: 		BRIDGE1_ENABLE = 1;
	BSF         LATB+0, 5 
;garage.c,163 :: 		BRIDGE2_ENABLE = 1;
	BSF         LATD+0, 1 
;garage.c,165 :: 		PWM1_Set_Duty(80);
	MOVLW       80
	MOVWF       FARG_PWM1_Set_Duty_new_duty+0 
	CALL        _PWM1_Set_Duty+0, 0
;garage.c,166 :: 		PWM1_Start();
	CALL        _PWM1_Start+0, 0
;garage.c,167 :: 		}
L_end_Door_Open_Slow:
	RETURN      0
; end of _Door_Open_Slow

_Door_Close:

;garage.c,170 :: 		void Door_Close()
;garage.c,172 :: 		BRIDGE1_ENABLE = 1;
	BSF         LATB+0, 5 
;garage.c,173 :: 		BRIDGE2_ENABLE = 1;
	BSF         LATD+0, 1 
;garage.c,175 :: 		PWM2_Set_Duty(90);
	MOVLW       90
	MOVWF       FARG_PWM2_Set_Duty_new_duty+0 
	CALL        _PWM2_Set_Duty+0, 0
;garage.c,176 :: 		PWM2_Start();
	CALL        _PWM2_Start+0, 0
;garage.c,177 :: 		}
L_end_Door_Close:
	RETURN      0
; end of _Door_Close

_Door_Close_Slow:

;garage.c,180 :: 		void Door_Close_Slow()
;garage.c,182 :: 		BRIDGE1_ENABLE = 1;
	BSF         LATB+0, 5 
;garage.c,183 :: 		BRIDGE2_ENABLE = 1;
	BSF         LATD+0, 1 
;garage.c,185 :: 		PWM2_Set_Duty(80);
	MOVLW       80
	MOVWF       FARG_PWM2_Set_Duty_new_duty+0 
	CALL        _PWM2_Set_Duty+0, 0
;garage.c,186 :: 		PWM2_Start();
	CALL        _PWM2_Start+0, 0
;garage.c,187 :: 		}
L_end_Door_Close_Slow:
	RETURN      0
; end of _Door_Close_Slow

_Interrupt_Init:

;garage.c,190 :: 		void Interrupt_Init()
;garage.c,193 :: 		INTCON.GIE = 1;
	BSF         INTCON+0, 7 
;garage.c,196 :: 		INTCON.PEIE = 1;
	BSF         INTCON+0, 6 
;garage.c,199 :: 		INTCON.TMR0IF = 0;
	BCF         INTCON+0, 2 
;garage.c,200 :: 		INTCON.TMR0IE = 1;
	BSF         INTCON+0, 5 
;garage.c,203 :: 		INTCON3.INT1IF = 0;
	BCF         INTCON3+0, 0 
;garage.c,204 :: 		INTCON2.INTEDG1 = 1;
	BSF         INTCON2+0, 5 
;garage.c,205 :: 		INTCON3.INT1IE = 1;
	BSF         INTCON3+0, 3 
;garage.c,208 :: 		INTCON3.INT2IF = 0;
	BCF         INTCON3+0, 1 
;garage.c,209 :: 		INTCON2.INTEDG2 = 1;
	BSF         INTCON2+0, 4 
;garage.c,210 :: 		INTCON3.INT2IE = 1;
	BSF         INTCON3+0, 4 
;garage.c,211 :: 		}
L_end_Interrupt_Init:
	RETURN      0
; end of _Interrupt_Init

_Timer_Start:

;garage.c,214 :: 		void Timer_Start()
;garage.c,217 :: 		T0CON = 0b00000111;
	MOVLW       7
	MOVWF       T0CON+0 
;garage.c,218 :: 		TMR0L = 0x00;
	CLRF        TMR0L+0 
;garage.c,219 :: 		TMR0H = 0x00;
	CLRF        TMR0H+0 
;garage.c,220 :: 		INTCON.TMR0IE = 1;
	BSF         INTCON+0, 5 
;garage.c,221 :: 		T0CON.TMR0ON = 1;
	BSF         T0CON+0, 7 
;garage.c,222 :: 		}
L_end_Timer_Start:
	RETURN      0
; end of _Timer_Start

_Lights_On:

;garage.c,225 :: 		void Lights_On()
;garage.c,227 :: 		BULB = 1;
	BSF         LATA+0, 3 
;garage.c,228 :: 		LED_LIGHT1 = 1;
	BSF         LATA+0, 1 
;garage.c,229 :: 		LED_LIGHT2 = 1;
	BSF         LATA+0, 2 
;garage.c,232 :: 		Timer_Start();
	CALL        _Timer_Start+0, 0
;garage.c,233 :: 		}
L_end_Lights_On:
	RETURN      0
; end of _Lights_On

_main:

;garage.c,236 :: 		void main() {
;garage.c,238 :: 		cnt = 0;
	CLRF        _cnt+0 
;garage.c,240 :: 		MCU_Init();
	CALL        _MCU_Init+0, 0
;garage.c,241 :: 		Flags_Init();
	CALL        _Flags_Init+0, 0
;garage.c,242 :: 		Interrupt_Init();
	CALL        _Interrupt_Init+0, 0
;garage.c,244 :: 		Sleep_Start();
	CALL        _Sleep_Start+0, 0
;garage.c,246 :: 		while(1)
L_main5:
;garage.c,267 :: 		if (Button(&PORTB, 1, 1, 1))
	MOVLW       PORTB+0
	MOVWF       FARG_Button_port+0 
	MOVLW       hi_addr(PORTB+0)
	MOVWF       FARG_Button_port+1 
	MOVLW       1
	MOVWF       FARG_Button_pin+0 
	MOVLW       1
	MOVWF       FARG_Button_time_ms+0 
	MOVLW       1
	MOVWF       FARG_Button_active_state+0 
	CALL        _Button+0, 0
	MOVF        R0, 1 
	BTFSC       STATUS+0, 2 
	GOTO        L_main7
;garage.c,269 :: 		start_state = 1;
	BSF         _start_state+0, BitPos(_start_state+0) 
;garage.c,270 :: 		}
L_main7:
;garage.c,271 :: 		if (start_state && Button(&PORTB, 1, 1, 0))
	BTFSS       _start_state+0, BitPos(_start_state+0) 
	GOTO        L_main10
	MOVLW       PORTB+0
	MOVWF       FARG_Button_port+0 
	MOVLW       hi_addr(PORTB+0)
	MOVWF       FARG_Button_port+1 
	MOVLW       1
	MOVWF       FARG_Button_pin+0 
	MOVLW       1
	MOVWF       FARG_Button_time_ms+0 
	CLRF        FARG_Button_active_state+0 
	CALL        _Button+0, 0
	MOVF        R0, 1 
	BTFSC       STATUS+0, 2 
	GOTO        L_main10
L__main76:
;garage.c,273 :: 		if(mode >= 0 && mode < 3)
	MOVLW       0
	SUBWF       _mode+0, 0 
	BTFSS       STATUS+0, 0 
	GOTO        L_main13
	MOVLW       3
	SUBWF       _mode+0, 0 
	BTFSC       STATUS+0, 0 
	GOTO        L_main13
L__main75:
;garage.c,275 :: 		mode ++;
	INCF        _mode+0, 1 
;garage.c,276 :: 		}
	GOTO        L_main14
L_main13:
;garage.c,277 :: 		else if(mode == 3)
	MOVF        _mode+0, 0 
	XORLW       3
	BTFSS       STATUS+0, 2 
	GOTO        L_main15
;garage.c,279 :: 		mode = 0;
	CLRF        _mode+0 
;garage.c,280 :: 		}
	GOTO        L_main16
L_main15:
;garage.c,283 :: 		mode = 0;
	CLRF        _mode+0 
;garage.c,284 :: 		}
L_main16:
L_main14:
;garage.c,285 :: 		Lights_On();
	CALL        _Lights_On+0, 0
;garage.c,286 :: 		start_state = 0;
	BCF         _start_state+0, BitPos(_start_state+0) 
;garage.c,287 :: 		}
L_main10:
;garage.c,290 :: 		if (Button(&PORTB, 2, 1, 1))
	MOVLW       PORTB+0
	MOVWF       FARG_Button_port+0 
	MOVLW       hi_addr(PORTB+0)
	MOVWF       FARG_Button_port+1 
	MOVLW       2
	MOVWF       FARG_Button_pin+0 
	MOVLW       1
	MOVWF       FARG_Button_time_ms+0 
	MOVLW       1
	MOVWF       FARG_Button_active_state+0 
	CALL        _Button+0, 0
	MOVF        R0, 1 
	BTFSC       STATUS+0, 2 
	GOTO        L_main17
;garage.c,292 :: 		start_state2 = 1;
	BSF         _start_state2+0, BitPos(_start_state2+0) 
;garage.c,293 :: 		}
L_main17:
;garage.c,294 :: 		if (start_state2 && Button(&PORTB, 2, 1, 0))
	BTFSS       _start_state2+0, BitPos(_start_state2+0) 
	GOTO        L_main20
	MOVLW       PORTB+0
	MOVWF       FARG_Button_port+0 
	MOVLW       hi_addr(PORTB+0)
	MOVWF       FARG_Button_port+1 
	MOVLW       2
	MOVWF       FARG_Button_pin+0 
	MOVLW       1
	MOVWF       FARG_Button_time_ms+0 
	CLRF        FARG_Button_active_state+0 
	CALL        _Button+0, 0
	MOVF        R0, 1 
	BTFSC       STATUS+0, 2 
	GOTO        L_main20
L__main74:
;garage.c,296 :: 		if(mode >= 0 && mode < 3)
	MOVLW       0
	SUBWF       _mode+0, 0 
	BTFSS       STATUS+0, 0 
	GOTO        L_main23
	MOVLW       3
	SUBWF       _mode+0, 0 
	BTFSC       STATUS+0, 0 
	GOTO        L_main23
L__main73:
;garage.c,298 :: 		mode ++;
	INCF        _mode+0, 1 
;garage.c,299 :: 		}
	GOTO        L_main24
L_main23:
;garage.c,300 :: 		else if(mode == 3)
	MOVF        _mode+0, 0 
	XORLW       3
	BTFSS       STATUS+0, 2 
	GOTO        L_main25
;garage.c,302 :: 		mode = 0;
	CLRF        _mode+0 
;garage.c,303 :: 		}
	GOTO        L_main26
L_main25:
;garage.c,306 :: 		mode = 0;
	CLRF        _mode+0 
;garage.c,307 :: 		}
L_main26:
L_main24:
;garage.c,308 :: 		Lights_On();
	CALL        _Lights_On+0, 0
;garage.c,309 :: 		start_state2 = 0;
	BCF         _start_state2+0, BitPos(_start_state2+0) 
;garage.c,310 :: 		}
L_main20:
;garage.c,313 :: 		if(Button(&PORTB, 4, 1, 1))
	MOVLW       PORTB+0
	MOVWF       FARG_Button_port+0 
	MOVLW       hi_addr(PORTB+0)
	MOVWF       FARG_Button_port+1 
	MOVLW       4
	MOVWF       FARG_Button_pin+0 
	MOVLW       1
	MOVWF       FARG_Button_time_ms+0 
	MOVLW       1
	MOVWF       FARG_Button_active_state+0 
	CALL        _Button+0, 0
	MOVF        R0, 1 
	BTFSC       STATUS+0, 2 
	GOTO        L_main27
;garage.c,315 :: 		door_down = 1;
	BSF         _door_down+0, BitPos(_door_down+0) 
;garage.c,316 :: 		}
L_main27:
;garage.c,317 :: 		if(door_down && Button(&PORTB, 4, 1, 0))
	BTFSS       _door_down+0, BitPos(_door_down+0) 
	GOTO        L_main30
	MOVLW       PORTB+0
	MOVWF       FARG_Button_port+0 
	MOVLW       hi_addr(PORTB+0)
	MOVWF       FARG_Button_port+1 
	MOVLW       4
	MOVWF       FARG_Button_pin+0 
	MOVLW       1
	MOVWF       FARG_Button_time_ms+0 
	CLRF        FARG_Button_active_state+0 
	CALL        _Button+0, 0
	MOVF        R0, 1 
	BTFSC       STATUS+0, 2 
	GOTO        L_main30
L__main72:
;garage.c,319 :: 		door_down = 0;
	BCF         _door_down+0, BitPos(_door_down+0) 
;garage.c,320 :: 		}
L_main30:
;garage.c,322 :: 		if(Button(&PORTB, 3, 1, 1))
	MOVLW       PORTB+0
	MOVWF       FARG_Button_port+0 
	MOVLW       hi_addr(PORTB+0)
	MOVWF       FARG_Button_port+1 
	MOVLW       3
	MOVWF       FARG_Button_pin+0 
	MOVLW       1
	MOVWF       FARG_Button_time_ms+0 
	MOVLW       1
	MOVWF       FARG_Button_active_state+0 
	CALL        _Button+0, 0
	MOVF        R0, 1 
	BTFSC       STATUS+0, 2 
	GOTO        L_main31
;garage.c,324 :: 		door_up = 1;
	BSF         _door_up+0, BitPos(_door_up+0) 
;garage.c,325 :: 		}
L_main31:
;garage.c,326 :: 		if(door_up && Button(&PORTB, 3, 1, 0))
	BTFSS       _door_up+0, BitPos(_door_up+0) 
	GOTO        L_main34
	MOVLW       PORTB+0
	MOVWF       FARG_Button_port+0 
	MOVLW       hi_addr(PORTB+0)
	MOVWF       FARG_Button_port+1 
	MOVLW       3
	MOVWF       FARG_Button_pin+0 
	MOVLW       1
	MOVWF       FARG_Button_time_ms+0 
	CLRF        FARG_Button_active_state+0 
	CALL        _Button+0, 0
	MOVF        R0, 1 
	BTFSC       STATUS+0, 2 
	GOTO        L_main34
L__main71:
;garage.c,328 :: 		door_up = 0;
	BCF         _door_up+0, BitPos(_door_up+0) 
;garage.c,329 :: 		}
L_main34:
;garage.c,332 :: 		if(Button(&PORTE, 0, 1, 1))
	MOVLW       PORTE+0
	MOVWF       FARG_Button_port+0 
	MOVLW       hi_addr(PORTE+0)
	MOVWF       FARG_Button_port+1 
	CLRF        FARG_Button_pin+0 
	MOVLW       1
	MOVWF       FARG_Button_time_ms+0 
	MOVLW       1
	MOVWF       FARG_Button_active_state+0 
	CALL        _Button+0, 0
	MOVF        R0, 1 
	BTFSC       STATUS+0, 2 
	GOTO        L_main35
;garage.c,334 :: 		slow_closing = 1;
	BSF         _slow_closing+0, BitPos(_slow_closing+0) 
;garage.c,336 :: 		if(mode == 3)
	MOVF        _mode+0, 0 
	XORLW       3
	BTFSS       STATUS+0, 2 
	GOTO        L_main36
;garage.c,338 :: 		zoneA = 1;
	BSF         _zoneA+0, BitPos(_zoneA+0) 
;garage.c,339 :: 		zoneB = 0;
	BCF         _zoneB+0, BitPos(_zoneB+0) 
;garage.c,340 :: 		}
L_main36:
;garage.c,341 :: 		}
L_main35:
;garage.c,343 :: 		if(slow_closing && Button(&PORTE, 0, 1, 0))
	BTFSS       _slow_closing+0, BitPos(_slow_closing+0) 
	GOTO        L_main39
	MOVLW       PORTE+0
	MOVWF       FARG_Button_port+0 
	MOVLW       hi_addr(PORTE+0)
	MOVWF       FARG_Button_port+1 
	CLRF        FARG_Button_pin+0 
	MOVLW       1
	MOVWF       FARG_Button_time_ms+0 
	CLRF        FARG_Button_active_state+0 
	CALL        _Button+0, 0
	MOVF        R0, 1 
	BTFSC       STATUS+0, 2 
	GOTO        L_main39
L__main70:
;garage.c,346 :: 		if(mode == 1)
	MOVF        _mode+0, 0 
	XORLW       1
	BTFSS       STATUS+0, 2 
	GOTO        L_main40
;garage.c,348 :: 		zoneA = 0;
	BCF         _zoneA+0, BitPos(_zoneA+0) 
;garage.c,349 :: 		zoneB = 1;
	BSF         _zoneB+0, BitPos(_zoneB+0) 
;garage.c,350 :: 		}
L_main40:
;garage.c,351 :: 		slow_closing = 0;
	BCF         _slow_closing+0, BitPos(_slow_closing+0) 
;garage.c,352 :: 		}
L_main39:
;garage.c,355 :: 		if(Button(&PORTE, 1, 1, 1))
	MOVLW       PORTE+0
	MOVWF       FARG_Button_port+0 
	MOVLW       hi_addr(PORTE+0)
	MOVWF       FARG_Button_port+1 
	MOVLW       1
	MOVWF       FARG_Button_pin+0 
	MOVLW       1
	MOVWF       FARG_Button_time_ms+0 
	MOVLW       1
	MOVWF       FARG_Button_active_state+0 
	CALL        _Button+0, 0
	MOVF        R0, 1 
	BTFSC       STATUS+0, 2 
	GOTO        L_main41
;garage.c,358 :: 		if(mode == 1)
	MOVF        _mode+0, 0 
	XORLW       1
	BTFSS       STATUS+0, 2 
	GOTO        L_main42
;garage.c,360 :: 		zoneB = 0;
	BCF         _zoneB+0, BitPos(_zoneB+0) 
;garage.c,361 :: 		zoneC = 1;
	BSF         _zoneC+0, BitPos(_zoneC+0) 
;garage.c,362 :: 		}
L_main42:
;garage.c,363 :: 		slow_opening = 1;
	BSF         _slow_opening+0, BitPos(_slow_opening+0) 
;garage.c,364 :: 		}
L_main41:
;garage.c,366 :: 		if(slow_opening && Button(&PORTE, 1, 1, 0))
	BTFSS       _slow_opening+0, BitPos(_slow_opening+0) 
	GOTO        L_main45
	MOVLW       PORTE+0
	MOVWF       FARG_Button_port+0 
	MOVLW       hi_addr(PORTE+0)
	MOVWF       FARG_Button_port+1 
	MOVLW       1
	MOVWF       FARG_Button_pin+0 
	MOVLW       1
	MOVWF       FARG_Button_time_ms+0 
	CLRF        FARG_Button_active_state+0 
	CALL        _Button+0, 0
	MOVF        R0, 1 
	BTFSC       STATUS+0, 2 
	GOTO        L_main45
L__main69:
;garage.c,369 :: 		if(mode == 3)
	MOVF        _mode+0, 0 
	XORLW       3
	BTFSS       STATUS+0, 2 
	GOTO        L_main46
;garage.c,371 :: 		zoneB = 1;
	BSF         _zoneB+0, BitPos(_zoneB+0) 
;garage.c,372 :: 		zoneC = 0;
	BCF         _zoneC+0, BitPos(_zoneC+0) 
;garage.c,373 :: 		}
L_main46:
;garage.c,374 :: 		slow_opening = 0;
	BCF         _slow_opening+0, BitPos(_slow_opening+0) 
;garage.c,375 :: 		}
L_main45:
;garage.c,380 :: 		if(mode == 0)
	MOVF        _mode+0, 0 
	XORLW       0
	BTFSS       STATUS+0, 2 
	GOTO        L_main47
;garage.c,382 :: 		Door_Stop();
	CALL        _Door_Stop+0, 0
;garage.c,383 :: 		}
L_main47:
;garage.c,385 :: 		if(mode == 1)
	MOVF        _mode+0, 0 
	XORLW       1
	BTFSS       STATUS+0, 2 
	GOTO        L_main48
;garage.c,388 :: 		if(!zoneC && !door_up)
	BTFSC       _zoneC+0, BitPos(_zoneC+0) 
	GOTO        L_main51
	BTFSC       _door_up+0, BitPos(_door_up+0) 
	GOTO        L_main51
L__main68:
;garage.c,390 :: 		Door_Open();
	CALL        _Door_Open+0, 0
;garage.c,391 :: 		}
L_main51:
;garage.c,393 :: 		if(zoneC && !door_up)
	BTFSS       _zoneC+0, BitPos(_zoneC+0) 
	GOTO        L_main54
	BTFSC       _door_up+0, BitPos(_door_up+0) 
	GOTO        L_main54
L__main67:
;garage.c,395 :: 		Door_Open_Slow();
	CALL        _Door_Open_Slow+0, 0
;garage.c,396 :: 		}
L_main54:
;garage.c,397 :: 		if(door_up)
	BTFSS       _door_up+0, BitPos(_door_up+0) 
	GOTO        L_main55
;garage.c,399 :: 		mode = 2;
	MOVLW       2
	MOVWF       _mode+0 
;garage.c,400 :: 		}
L_main55:
;garage.c,401 :: 		}
L_main48:
;garage.c,403 :: 		if(mode == 2)
	MOVF        _mode+0, 0 
	XORLW       2
	BTFSS       STATUS+0, 2 
	GOTO        L_main56
;garage.c,405 :: 		Door_Stop();
	CALL        _Door_Stop+0, 0
;garage.c,406 :: 		}
L_main56:
;garage.c,408 :: 		if(mode == 3)
	MOVF        _mode+0, 0 
	XORLW       3
	BTFSS       STATUS+0, 2 
	GOTO        L_main57
;garage.c,411 :: 		if(!zoneA && !door_down)
	BTFSC       _zoneA+0, BitPos(_zoneA+0) 
	GOTO        L_main60
	BTFSC       _door_down+0, BitPos(_door_down+0) 
	GOTO        L_main60
L__main66:
;garage.c,413 :: 		Door_Close();
	CALL        _Door_Close+0, 0
;garage.c,414 :: 		}
L_main60:
;garage.c,416 :: 		if(zoneA && !door_down)
	BTFSS       _zoneA+0, BitPos(_zoneA+0) 
	GOTO        L_main63
	BTFSC       _door_down+0, BitPos(_door_down+0) 
	GOTO        L_main63
L__main65:
;garage.c,418 :: 		Door_Close_Slow();
	CALL        _Door_Close_Slow+0, 0
;garage.c,419 :: 		}
L_main63:
;garage.c,420 :: 		if(door_down)
	BTFSS       _door_down+0, BitPos(_door_down+0) 
	GOTO        L_main64
;garage.c,422 :: 		mode = 0;
	CLRF        _mode+0 
;garage.c,423 :: 		}
L_main64:
;garage.c,424 :: 		}
L_main57:
;garage.c,426 :: 		}//while loop
	GOTO        L_main5
;garage.c,428 :: 		}// main loop
L_end_main:
	GOTO        $+0
; end of _main

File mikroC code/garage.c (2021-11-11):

/*
   Project:    Garage Door Control Unit
   MCU:        PIC18F45K22
   Hardware:   Garage Door Control PCB Card
   Author:     Mario Oletiæ
   
   Project description:
   -----------------------------------------------------------------------------
   This project is developed (both hardware and software) for replacing/retrofit
   of the old garage door PCB. PCB has six input signals (24VDC level). Two of 
   them are used for starting the door movements (opening or closing). Doors can
   be started with radio switch (Input1) with 24VDC signal output or some other 
   common switch (Input2). Other four inputs are used for external capacitive or
   inductive sensors to determine door position - two for UP and DOWN positions 
   and two to determine a position of doors while approaching CLOSE or OPEN 
   positions. The last two positions are used for slowing down the doors. 
   Signals on INPUT1 and INPUT2 are switching between four working modes. MODE 0 
   and MODE2 are for stoping, MODE1 for opening and MODE3 for closing the doors.
   Outputs are used for controlling the 24V DC motor with PWM signals. Depending 
   on the door position, the motor can rotate with two different speeds (speed 
   depends on the PWM duty cycle) - one is for normal door speed and the other 
   (slower) is for approaching final positions. Also, when activating the door, 
   lights turn on. There are two outputs for 24V DC LED lights and one output 
   for 230V AC light bulb which is controlled via Triac. Triac is triggered with 
   OptoTriac IC with zero-cross detection circuit. Also, OptoTriac isolates 230V 
   AC system from the rest of the PCB low voltage systems. Lights will be turned 
   off after doors are stoped, no matter in what position, after a fixed period 
   of time passes. When doors are not moving, MCU goes into sleep mode with much 
   lower current consumption. When a new signal for activating the doors appears, 
   MCU wakes up. On the PCB there is also mikroBUS connector, for possible future 
   upgrades with BLE or WiFi technologies so the door can be controlled through 
   PC or Smartphone Apps.
*/

unsigned short mode;
unsigned short cnt;
bit start_state, start_state2;
bit door_down, door_up, slow_opening, slow_closing;
bit zoneA, zoneB, zoneC;
sbit BRIDGE1_ENABLE at LATB.B5;
sbit BRIDGE2_ENABLE at LATD.B1;
sbit DIRECTION1 at LATC.B2;
sbit DIRECTION2 at LATC.B1;
sbit BULB at LATA.B3;
sbit LED_LIGHT1 at LATA.B1;
sbit LED_LIGHT2 at LATA.B2;

// Function sends MCU in sleep mode
void Sleep_Start()
{
   OSCCON.IDLEN = 0;
   asm sleep;
}

// Intrrupt function
void interrupt()
{
   // TMR0 Interrupt
   if(INTCON.TMR0IF)
   {
       cnt++;
       
       TMR0L = 0x00;
       TMR0H = 0x00;
       
       if(cnt >= 1)
       {
       // Stop Timer0
       T0CON.TMR0ON = 0;
       
       // Turn off the lights
       BULB = 0;
       LED_LIGHT1 = 0;
       LED_LIGHT2 = 0;
       
       Sleep_Start();
       
       cnt = 0;
       }
       INTCON.TMR0IF = 0;
   }
   
   // External Interrupt INT1
   if(INTCON3.INT1IF)
   {
      INTCON3.INT1IF = 0;
   }
   
   // External Interrupt INT2
   if(INTCON3.INT2IF)
   {
      INTCON3.INT2IF = 0;
   }
}


void MCU_Init()
{
   ANSELA=0x00;
   ANSELB=0x00;
   ANSELC=0x00;
   ANSELD=0x00;
   ANSELE=0x00;
   TRISA=0x00;
   TRISB=0b00011111;
   TRISC=0x00;
   TRISD=0x00;
   TRISE=0b00000011;
   LATA=0x00;
   LATB=0x00;
   LATC=0x00;
   LATD=0x00;
   LATE=0x00;
   
   PWM1_Init(5000);
   PWM2_Init(5000);
   
   Delay_ms(150);
}

// Setting program flags
void Flags_Init()
{
   start_state = 0;
   start_state2 = 0;
   mode = 0;
   door_down = 0;
   door_up = 0;
   slow_opening = 0;
   slow_closing = 0;
   zoneA = 1;
   zoneB = 0;
   zoneC = 0;
}

// Function stops motors
void Door_Stop()
{
   PWM1_Stop();
   PWM2_Stop();

   BRIDGE1_ENABLE = 0;
   BRIDGE2_ENABLE = 0;
   DIRECTION1 = 0;
   DIRECTION2 = 0;
}

// Function for opening the door
void Door_Open()
{
   BRIDGE1_ENABLE = 1;
   BRIDGE2_ENABLE = 1;

   PWM1_Set_Duty(90);
   PWM1_Start();
}

// Function for slow opening approach
void Door_Open_Slow()
{
   BRIDGE1_ENABLE = 1;
   BRIDGE2_ENABLE = 1;

   PWM1_Set_Duty(80);
   PWM1_Start();
}

// Function for closing the door
void Door_Close()
{
   BRIDGE1_ENABLE = 1;
   BRIDGE2_ENABLE = 1;

   PWM2_Set_Duty(90);
   PWM2_Start();
}

// Function for slow closing approach
void Door_Close_Slow()
{
   BRIDGE1_ENABLE = 1;
   BRIDGE2_ENABLE = 1;

   PWM2_Set_Duty(80);
   PWM2_Start();
}

// Interrupt initialisation
void Interrupt_Init()
{
   // Global Interrupt Enable
   INTCON.GIE = 1;
   
   // Peripheral Interrupt Enable
   INTCON.PEIE = 1;
   
   // TMR0 Interrupt
   INTCON.TMR0IF = 0;
   INTCON.TMR0IE = 1;
   
   // External Interrupt INT1
   INTCON3.INT1IF = 0;
   INTCON2.INTEDG1 = 1;
   INTCON3.INT1IE = 1;
   
   // External Interrupt INT2
   INTCON3.INT2IF = 0;
   INTCON2.INTEDG2 = 1;
   INTCON3.INT2IE = 1;
}

// Seting the timer for lights
void Timer_Start()
{
   //Prescaler 1:256
   T0CON = 0b00000111;
   TMR0L = 0x00;
   TMR0H = 0x00;
   INTCON.TMR0IE = 1;
   T0CON.TMR0ON = 1;
}

// Turn on the lights
void Lights_On()
{
   BULB = 1;
   LED_LIGHT1 = 1;
   LED_LIGHT2 = 1;
   
   // Start Timer0
   Timer_Start();
}
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
